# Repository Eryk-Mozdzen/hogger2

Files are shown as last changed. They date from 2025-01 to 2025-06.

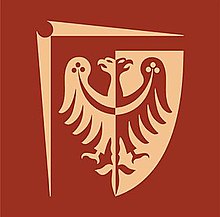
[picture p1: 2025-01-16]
hardware/resources/pwr.jpg

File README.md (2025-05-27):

# Two HOG wheel robot Hogger^2

Hogger^2 is mobile robot with two HOG ([Hemispherical Omnidirectional Gimbaled](https://en.wikipedia.org/wiki/Hemispherical_omnidirectional_gimbaled_wheel)) wheels.

- kinematic models were derived by Paweł Joniak in his [engineering thesis](https://kcir.pwr.edu.pl/~mucha/Pracki/Pawel_Joniak_praca_magisterska.pdf) (2014)
- chassis was originally created by Damian Góral in his [engineering thesis](https://kcir.pwr.edu.pl/~mucha/Pracki/Damian_Goral_praca_inzynierska.pdf) (2017)
- control algorithms were designed by Paweł Joniak in his [master thesis](https://kcir.pwr.edu.pl/~mucha/Pracki/Pawel_Joniak_praca_magisterska.pdf) (2017)
- code generation technique was proposed by Jędrzej Boczar in his [master thesis](https://kcir.pwr.edu.pl/~mucha/Pracki/Jedrzej_Boczar_praca_magisterska.pdf) (2019)
- JSON based communication was proposed by Tomasz Lubelski in his [engineering thesis](https://kcir.pwr.edu.pl/~mucha/Pracki/Tomek_Lubelski_praca_inzynierska.pdf) (2023)

## CAD project

CAD files are developed using Onshape [here](https://cad.onshape.com/documents/57202b77900f6c62ca0efc3a/w/393cd826dd9c91d9b304b9f8/e/825e632008c05703f420ee31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).

## Hardware overview



## Software overview



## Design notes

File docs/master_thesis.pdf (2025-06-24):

## Wrocław University of Science and Technology Faculty of Electronics, Photonics and Microsystems

### Field of Study: Control Engineering and Robotics (AIR)

# MASTER THESIS

## Title of Thesis:

### Control system for two HOG wheel mobile robot

## Author:

### Eryk Możdżeń

## Supervisor:

Robert Muszyński PhD,

### Department of Cybernetics and Robotics

### WROCŁAW 2025

# Contents

1 Introduction | 3
2 Platform description | 5
3 Control algorithms | 27
4 Experiments | 36
5 Summary | 70
Bibliography | 72
A Electronic schematic | 76

Contents | 2
B Motor controller tunning | 84
C Cascade PID tunning | 86

For typesetting this thesis, the LATEX document preparation system has been used. LATEX has been developed by L. Lamport [Lam94], and is an overlay on top of the TEX system [Knu86a, Knu86b]. Mathematical fonts called AMS Euler which have been used in this document, have been commissioned by the American Mathematical Society and designed by H. Zapf [KZ86] with the assistance of D. Knuth and his students. The text font, called URW Palladio, is a clone of the Zapf font family named Palatino [LPn05], and in the author’s opinion, it harmonizes exceptionally well with the design of the AMS Euler font. The authors of the thesis template are R. Muszyński and R. Orozco [MO22], who utilized the mgr.cls document class created by A. Ratajczak [Rat08].

[Knu86a] D. E. Knuth, The TEX book, volume A of Computers and Typesetting. Addison-Wesley, Reading, 1986.

[Knu86b] D. E. Knuth, TEX: The Program, volume B of Computers and Typesetting. Addison-Wesley, Reading, 1986.

[KZ86] D. E. Knuth, H. Zapf, AMS Euler — A new typeface for mathematics. Scholary Publishing, 20:131–157, 1986.

[Lam94] L. Lamport, LATEX: A Document Preparation System. Addison--Wesley, Reading, 1994.

[LPn05] Linotype Palatino nova: A classical typeface redesigned by Hermann Zapf, Linotype Library GmbH, 2005.

[MO22] R. Muszyński, R. Orozco, Examples and formatting guidelines for a
thesis. https://kcir.pwr.edu.pl/~mucha/Pracki/praca_dyplomowa_wzor.
pdf, (https://kcir.pwr.edu.pl/~mucha/Pracki/praca_dyplomowa_wzor.pdf) 2022.

[Rat08] A. Ratajczak, Document class – mgr.cls. http://diablo.kcir.pwr.edu.pl/
~ar/LaTeX/mgr.php, (http://diablo.kcir.pwr.edu.pl/~ar/LaTeX/mgr.php) 2008.

# Chapter 1

# Introduction

Nowadays, mobile robotic systems are widely used to manage warehouses and to support production lines in factories around the world. Robots often operate in well-known environments specifically prepared for their operation, e.g., mobile robots on flat concrete floors in warehouses. In order to perform agile movements on flat ground, it is common to use omnidirectional wheels as the main drive system for UGV platforms [KSBT⁺17].
The Hemispherical Omnidirectional Gimballed (HOG) wheel from 1938 [mec38], called also “Singularity Drive System”, has been a topic of research in robotics applications in the past few years [Ack, Ryb13, Jon14, Jon17, Boc19]. In theory, the use of constantly rotating hemispheres, each with a variable orientation, enables motion with high acceleration in any chosen direction. Additionally, massive hemispheres with high inertia can act as a kinetic energy bank for the platform, allowing the use of less powerful motors without compromising the robot’s agility.
A similar type of propulsion can be observed in power troweling machines, which are widely used in the finishing of concrete surfaces. This branch of the industry has already been robotized, and examples of such robots are presented in Figure 1.1. In contrast, the HOG drive relies on a single point of contact with the ground, which has the advantage of allowing a relatively simple mathematical description of the system. Nevertheless, sufficiently large hemispheres should also operate reliably in muddy and sandy environments, similarly to trowelling machines.
The goal of this thesis is to modernize the existing mechanical design of a two HOG wheel mobile robot, develop a hardware platform that enables the implementation of advanced control algorithms for such a robot, and conduct a qualitative analysis of the performance of selected control algorithms that had previously been tested in simulation environments only. The content of this work is organized as follows. Chapter 2 contains a description of the robot, including mechanical modifications, and custom controller module. The description of the tested algorithms are presented in Chapter 3. Chapter 4 presents the results of the conducted experiments along with detailed conclusions. Chapter 5 contains a summary and the key conclusions drawn from working with the HOG drive technology.

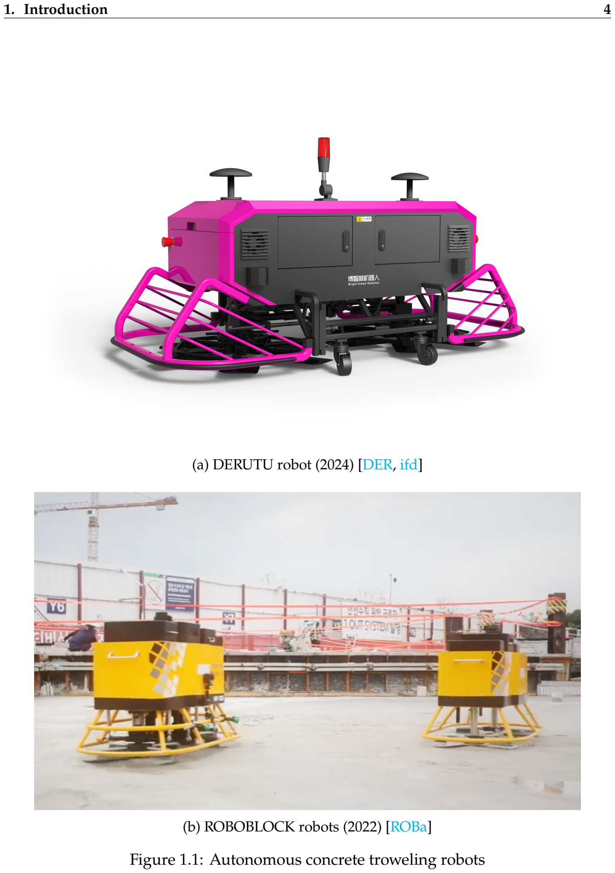
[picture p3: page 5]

1. Introduction | 4
(a) DERUTU robot (2024) [DER, ifd]
(b) ROBOBLOCK robots (2022) [ROBa]

Figure 1.1: Autonomous concrete troweling robots

# Chapter 2

# Platform description

Robots with two HOG wheels are not widely available. For the purposes of this work, the Hogger²
robot (shown in Figure 2.1) originally designed and elaborated as a part of the thesis [Gór17] was expanded and redesigned. This chapter includes the description of the dedicated electronic controller module, the developed software, the mechanical modifications and solutions of other issues identified during the development.
A HOG wheel, shown in Figure 2.2, it a type of drive system that allows movement in any direction using constantly spinning hemisphere, or part of it. In perfect conditions, hemisphere touches the ground in exactly one contact point P. By tilting the axis of rotation from the vertical position by small amount α, one can directly control the point of contact with the ground, effectively creating a wheel with variable radius r, angular velocity ω, and heading (not shown in Figure).
In the Hogger²
robot two HOG wheels are applied with an additional one passive Caster wheel that acts as a third support point. Assuming that the robot moves on a plane, it’s actual pose can be described using the coordinates x and y of the selected HOG wheel contact point and the orientation of the robot body. To obtain a complete robotic platform, it was necessary to equip the robot with perception and control systems.

## 2.1 Requirements, decisions and assumptions

Integrated controller circuit acts as central decision unit mounted on the robot body. First version of the hardware design was developed by the author as part of the “Intermediate Project” course and described in reports [Moż24, Moż25]. Electronics circuits design for the Hogger²
robot is shown in Figure 2.3. The design consist of main microcontroller control unit, actuators for two HOG wheels, sensors needed for environment perception, and additional microcontroller with wireless communication capabilities. The overall design reduced the number of wires between components to a useful minimum. Electronics schematic as well as PCB design of the controller module is attached in Appendix A.
From the control task point of view the robot consists of two BLDC motors, for spinning the hemispheres, and four servomotors, for tilting them. For the sake of simplicity and robustness, it was decided to incorporate the BLDC motor controllers as a part of

2. Platform description | 6

Figure 2.1: The original Hogger² robot [Gór17]

the controller module, rather than relying on off-the-shelf solutions. It was assumed that hemispheres should rotate at relatively high speeds, so a “sensorless” method for driving BLDC motors was selected [LCA]. This approach enables measurement of the motor’s actual velocity without the need to install additional encoders on the motor shaft.
In order to perform advanced trajectory tracking algorithms, information about current position and velocity of the robot and its joints must be available to the robot embedded microcontroller in real time. It was decided that the state vector would be estimated using sensor fusion techniques, without correction from external systems. A further reduction in wiring was achieved by placing most of the sensors inside the controller module itself, creating an all-in-one solution. Both the solutions are described below.

## 2.2 Mechanical modifications

In order to conduct experiments with the existing robotic platform, its components had to be supplemented and modified. Mechanical components added to the robot are shown in Figure 2.4. The optical sensor was mounted into conical part, shown in Figure 2.5, to maximize height above ground without limiting the field of view. The caster wheel, the third support point, was shifted away from the main body of the robot to achieve a stable construction. The 3S LiPo 2000 mAh battery was placed on the center wheel at the back to act as a counterweight to the optical sensor cone located at the front. The controller module casing, shown in Figure 2.6, was mounted on top of the robot using mainly existing mounting points.
The servo drives originally used in the robot were not capable of precise control of the gimbal axes. The PWM interface was not capable of sending telemetry containing the actual position and velocity values of the drives. As a replacement, four Dynamixel AX-12A [ROBb] servomotors were mounted to drive all gimbal axes. In addition, the existing damaged BLDC motors were replaced with KAVAN C2830-750 motors [KAV]. The connection between the motor shaft and the hemispherical wheel, shown in Fig-

2. Platform description | 7
(a) rotation axis is vertical – no movement
(b) small tilt
(c) bigger tilt

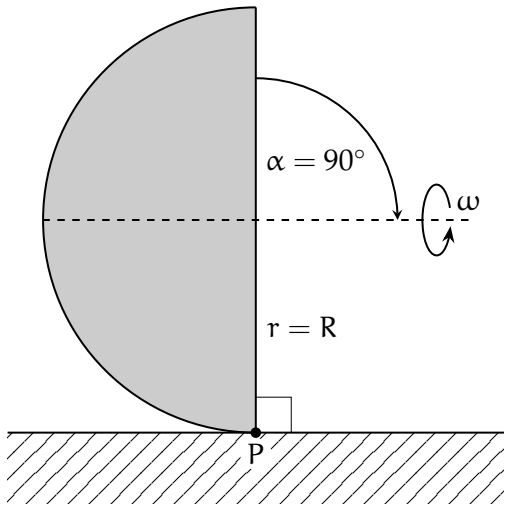
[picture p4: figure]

(d) maximum tilt – standard wheel

Figure 2.2: A HOG wheel tilting principle (cross section)

Figure 2.3: Electronic circuits of the Hogger²

Figure 2.4: Supplemented components

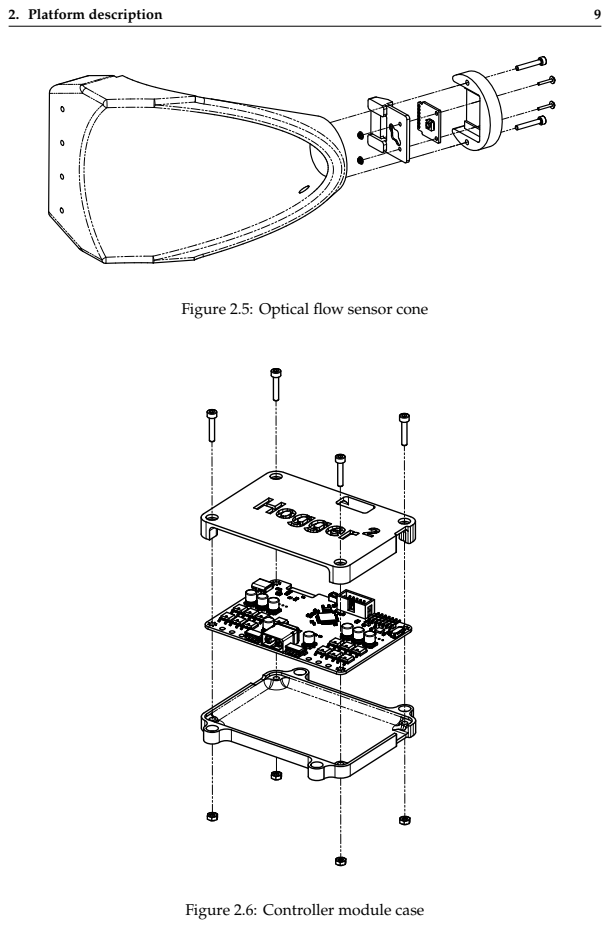
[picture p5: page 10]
2. Platform description

Figure 2.5: Optical flow sensor cone

Figure 2.6: Controller module case

2. Platform description | 10

Figure 2.7: Motor–hemisphere connection

ure 2.7, was redesigned to prevent looseness caused by vibrations. The threaded core allows for easy replacement of the wheel itself, enabling tests of how the hemisphere material affects the robot’s operation for future applications. Both thread directions are opposite to the desired wheel rotation, so the threads cannot unscrew themselves during normal ground operation. The existing silicone hemispheres were severely damaged at the point coinciding with the axis of rotation, so they were replaced with PLA 3D-printed parts. In summary, the mechanical construction is shown in Figure 2.8.

## 2.3 BLDC motor control

Brushless DC (BLDC) motors, due to their high durability, are the standard for modern robotic structures. Unlike conventional brushed motors, they require dedicated control algorithms to produce rotary motion. This section describes the sensorless control method used for the operation of the Hogger²
robot.

### 2.3.1 Source voltage inverters

A BLDC motor can be actuated by applying an alternating voltage pattern, commonly called the “six-step” algorithm [LCA] through its phases (U, V, W) via the source voltage inverter circuit shown in Figure 2.9. For practical reasons, the design consists of six separate power switches, arranged into three pairs (half-bridges) of upper (QUH, QVH, QWH) and lower (QUL, QVL, QWL) transistors. Automotive-grade IPD90N04S4L-04 N-channel MOSFETs [Inf] were used, along with LM2105D gate drivers [Ins] (not shown in Figure). Each half-bridge needs to be controlled by a pair of coupled PWM signals, resulting in a total of 12 control variables for both motors. To meet these requirements, the STM32H523 [STM] microcontroller was selected as a main control

2. Platform description | 11

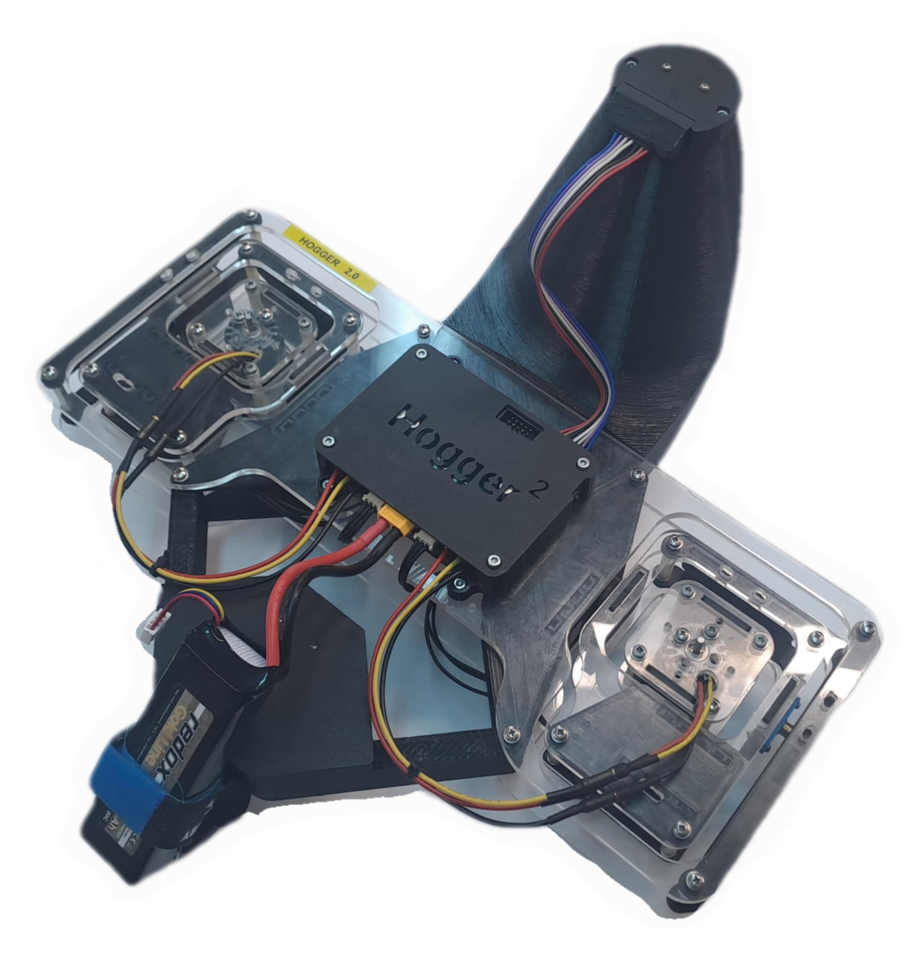
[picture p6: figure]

Figure 2.8: The Hogger²
robot after modifications

Figure 2.9: Source voltage inverter

2. Platform description | 12

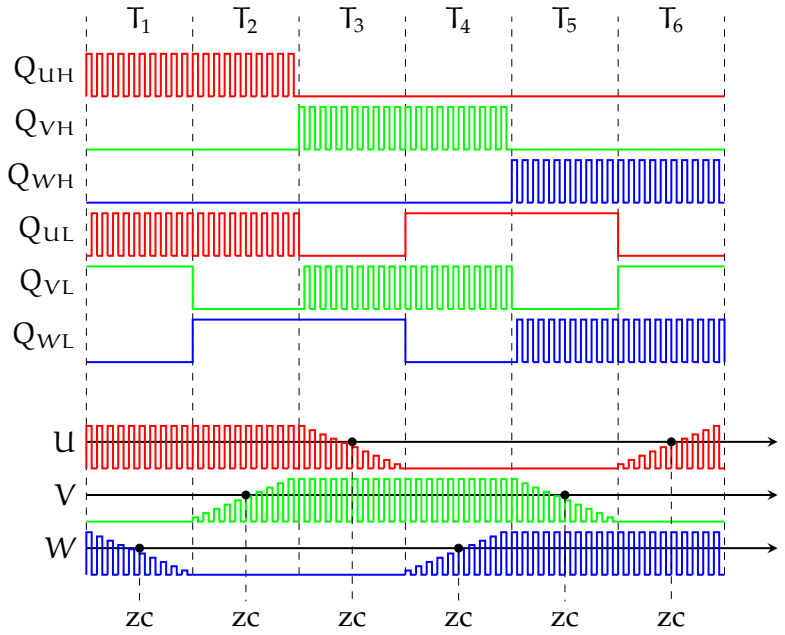
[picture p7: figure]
QUH; QVH; QWH; QUL; QVL; QWL

Figure 2.10: Six-step algorithm with back-EMF zero cross events

unit, as it includes two Advanced Control Timer peripherals dedicated to motor control applications.
The six-step algorithm, shown in Figure 2.10, considers an ordered sequence of control permutations T for switches Q. To obtain rotary motion, all steps must be applied in the sequence T1, T2, . . . , T6, T1, . . . for clockwise rotation, or T6, T5, . . . , T1, T6, . . . for counterclockwise rotation. Each step, also called a commutation, can configure each pair QxH and QxL to:
- connect the motor phase to the supply voltage (QxH high, QxL low),
- connect the motor phase to the ground (QxH low, QxL high),
- left the motor phase floating (QxH and QxL low).

Closing the upper and lower switches of the same half-bridge at the same time creates a short circuit and may damage the transistors. To prevent this situation, an additional 2 µs dead time was configured in the peripheral settings. In each step, one motor phase is powered, one is connected to ground, and the remaining floating phase is used to determine the next step through signal conditioning. For smooth control of the powered phase, 50 kHz center-aligned PWM modulation is applied to the upper and lower switches. Figure 2.11 presents oscillograms of phase and control signals for selected angular velocities. The described method aims to obtain a trapezoidal phase voltage waveform. In practical applications, the minimum angular velocity that the motor controller can handle is 125 rad

s without load, and 200 rad
s

during robot operation.
The maximum velocity is constrained by the motor itself. Empirical tests have shown that when the PWM duty cycle exceeds 80% with load, the motor begins to overheat significantly.

2. Platform description | 13
(a) angular velocity 200 rad
s
(b) angular velocity 250 rad
s
(c) angular velocity 500 rad
s
(d) angular velocity 664 rad
s

(80% duty cycle)

Figure 2.11: Oscillogram of QUH (yellow), QUL (blue), and U phase (red)

### 2.3.2 BEMF signal conditioning

Proper motor operation highly depends on the timing of the switching steps in the six-step algorithm. The rotor of the BLDC motor consists of an even number of magnets, forming an alternating magnetic field. By performing steps from T1 to T6, the rotor rotates through an angle called an electrical rotation, defined by one pair of magnets. To achieve a full 360◦ movement, called a mechanical rotation, the six-step algorithm must be performed n times (n electrical rotations), where n is the number of pole pairs in the rotor.
Each step represents ¹/6 of an electrical rotation, which equals 60◦
. During each step,
one winding coil is left floating, and the rotating magnets of the rotor induce a back electromotive force (BEMF) in it. Unfortunately, the BEMF voltage level is proportional to the angular velocity of the rotor, which implies that practical signal conditioning is only possible above a minimum shaft velocity. According to [LCA], the best motor performance is achieved by keeping the point where the BEMF voltage crosses the voltage at the motor’s coil interconnection (point N in Figure 2.9) in offset of 30◦ from
the beginning of each step. This point is called the zero-crossing event (ZC) and its precise localization is the greatest difficulty during implementation of the algorithm. The BEMF signal can be observed from the U, V, and W phases by the control unit using ADC through resistor dividers and small filtering capacitors. The neutral voltage

2. Platform description | 14

Timer; Advance Control Timer; ADC; six-step algorithm; PID; signal conditioning; Firmware; Peripherals; Update Event; Commutation Source; External Trigger Source; step duration; velocity; PWM duty cycle; step config; Commutation ISR; Injected Conversion Complete ISR; QVH; QUL; QUH; QVL; QWH; QWL

Figure 2.12: Controller implementation on the STM32H5

at point N can be calculated as the average of phase voltages

UN =

U + V + W
3

Controller implementation is presented in Figure 2.12. The STM32 ADC peripheral was synchronized with Advanced Control Timer to perform conversion in the middle of PWM high period using “Injected Conversion” feature. Then, on each PWM period, voltage from appropriate floating phase is compared with UN voltage by the software. To prevent false positive detections, the majority filter described in [LCA] was implemented. Result of each comparison is stored in the 8-bit variable acting as a shift register. If the number of positive comparisons (ones) is greater than the predefined threshold kth, then the ZC event occurs roughly 1
2

kthTPWM before the conversion starts. Using this knowledge, it is possible to calculate the time of next commutation in the sequence.
Unfortunately, under high motor load fluctuations experienced during movement using hemispheres, additional filtering was needed. In summary, period ti+1 of the next commutation Ti+1 can be calculated as

tizc = tconv −

1
2

kthTPWM

ti+1ideal = 2tizc

ti+1 = αtti+1ideal + (1 − αt)ti

,

where tconv is conversion start time (counted from the beginning of the step Ti), tizc is ZC event occur time, ti+1ideal is theoretical duration of next commutation, and ti+1 is duration that is applied in reality. For motors KAVAN 2830 750 KV parameters kth = 4, αt = 0.05 were found empirically.

2. Platform description | 15

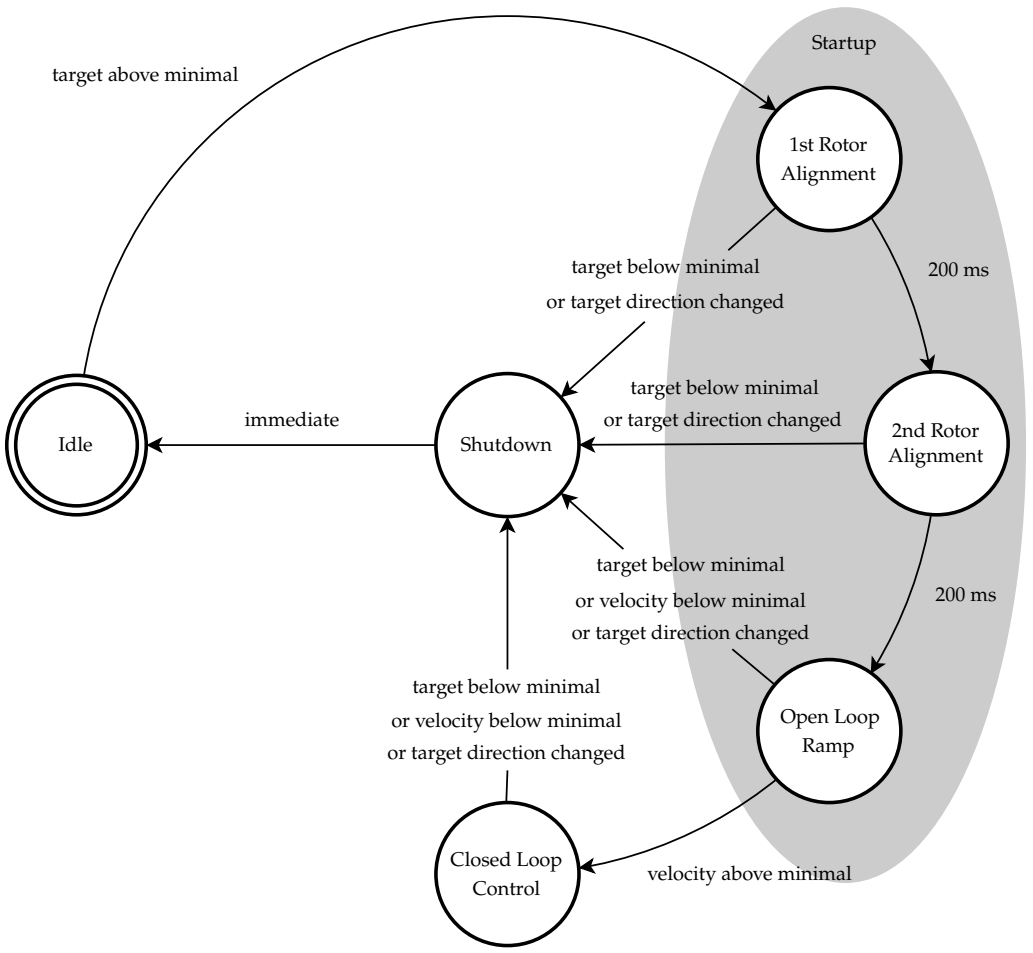
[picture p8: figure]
Idle; Open Loop Ramp; Closed Loop Control; Shutdown; Startup; 1st Rotor Alignment; 2nd Rotor Alignment; target above minimal; velocity above minimal; target below minimal; or velocity below minimal; or target direction changed; immediate

Figure 2.13: Motor controller state machine

Mechanical angular velocity of the motor shaft ω can be calculated and filtered by

ωzc = 2π

nzc

6pTzc
ωi+1 = αωωzc + (1 − αω)ωi

,

where ωzc is instantaneous angular velocity, ωi is filtered angular velocity, p is number of rotor pole pairs, and nzc is number of ZC events observed in time Tzc. For the selected motors p = 7, and empirical tests shown that parameters Tzc = 20 ms, αω = 0.1 are giving sufficiently good performance in practice.

### 2.3.3 Startup and closed-loop operation

The motor controller logic, presented in Figure 2.13, is defined by a finite state machine that handles motor startup, operation, and shutdown. The startup procedure consists of rotor alignment phases followed by a velocity ramp controlled in open-loop mode. The first rotor alignment stage sets the rotor to a known position by applying predefined commutation T1 for a specified duration. The second alignment ensures that

Figure 2.14: Geometric properties of the step response of an inertial system

the rotor spins in the correct direction by applying commutation T1 or T5, according to the desired direction. Both are performed using a PWM duty cycle of u = 30% over a 200 ms period.
When alignment is complete, a startup ramp is applied to accelerate the rotor to a point where BEMF signal conditioning becomes feasible. Subsequent commutations are applied to the inverter circuit, each with increasing frequency f and a constant PWM duty cycle of u = 40%. The ramp curve is defined as

f(t) = fmax
1 − e

−λt
,

where fmax = 1 kHz is the maximum commutation frequency, λ = 1 is the acceleration parameter, and t is the time elapsed since the beginning of the ramp. Empirical tests have shown that the proposed ramp provides more robust results than linear ramps and that the correct ramp shape is key to a successful startup. To ensure a smooth transition between open-loop and closed-loop control, a special blending function is used to merge both signals over a 1 second period after the ramp is complete.
The closed-loop operation is performed using a PID controller to maintain the motor’s angular velocity at the target value, using the PWM duty cycle u as the control input. For each motor, a PID controller was tuned using the Chien-Hrones-Reswick (CHR) method with 20% overshoot [ÅH95]. The results of the tuning procedures are included in Appendix B. The method, shown in Figure 2.14, involves drawing additional straight lines onto the step response (red plot) of an unknown inertial system, representing:
- the signal level at steady state before applying the step,
- the signal level at steady state after applying the step,
- the tangent line with the maximum slope (at point B).

Analysis of the line intersections reveals the basic geometric properties K (gain), T (time constant), and L (lag) of the simplified system, which approximates the plant.

2. Platform description | 17

These properties can be used to calculate PID parameters that ensure good closed-loop performance using the CHR 20% overshoot formulas

Kp = 0.95 T
KL
Ki = 0.68 1
KL
Kd = 0.45 T
K

To automate the process of obtaining PID settings from the step response, a Python script was created to find the parameters of the best-fitting four-parameter model in the form
Hm(s) = | Km (T1ms + 1)(T2ms + 1)
e

−Lms
,

which step response in the time domain is given by

hm(t) =

0 | t ⩽ Lm

Km

1 +

T2me

− t−Lm

T2m | − T1me − t−Lm
| T1m
T1m − T2m

!
| t > Lm

,

where T1m and T2m are time constants, Lm is a delay, and Km is the model gain. Using this model, it is possible to algebraically determine the point B, and ultimately extract the K, T, and L properties.

## 2.4 Sensor fusion

Reliable knowledge about robot state is a key to precise control. The robot x, y, θ coordinates are not possible to measure directly without external reference systems like GNSS or radio anchors [KCB⁺23]. Sensor fusion techniques allows for obtaining information about the system state from multiple measurement sources which is more reliable than each of the measurements separately. In this work an Extended Kalman Filter has been used for this purpose.

### 2.4.1 Extended Kalman Filter

In order to estimate the 2D pose of the robot using only on-board sensors, Extended Kalman Filter (EKF) [Wika] was developed. EKF is a sensor fusion technique that enables the estimation xˆ of the unknown state x of the discrete system in the form
xk = f(xk−1,uk−1) + ωk−1
zk = h(xk) + vk

,

where u are the system inputs, z are the measurements, and ω and v are process and observation noises, both assumed to be zero-mean Gaussian. In the following

2. Platform description | 18

description it is assumed that the system operates at fixed time intervals ∆t between time steps k.
The algorithm consists of two steps: prediction and correction. The prediction step can be defined as
xˆk|k−1 = f(xk−1|k−1,uk−1)
Pˆ
k|k−1 = FkPˆ
k−1|k−1F

T
k + Qk−1

,

where

Fk =

∂f
∂x
xˆ k−1|k−1
,uk

,

f is the system model, Q is the process noise covariance matrix, and Pˆ is the estimate of state vector covariance matrix. The notation xn|m represents the value of x at time n given observations from time periods where m ⩽ n. In this step, the input vector u can be obtained from sensors recording of relatively high-frequencies. It is crucial to perform the prediction step at fixed time intervals. Unfortunately, this implies prediction frequency to be equal to the sampling frequency of the slowest predicting sensor.
The correction step can be defined as
xˆk|k = xˆk|k−1 + Kk(zk − h(xˆk|k−1))
Pˆ

k|k = (I − KkHk)Pˆ
k|k−1

,

where
Kk = Pˆ

k|k−1Hk(HkPˆ
k|k−1H

T
k + Rk)

−1
,

Hk =

∂h
∂x
xˆ k|k−1

,

h is the sensor model, and R is the sensor noise covariance matrix. As opposed to the prediction step, the correction step can be performed separately for each correcting sensor. This effectively enables operation at the full sampling frequency of each sensor. Correcting measurements represent relatively low-frequency signals.

### 2.4.2 Estimator implementation

For the Hogger²
robot, the state vector x we will define as

x =

p θ p˙ θ γ ˙ m

T
=

x y θ x˙ y˙ θ γ ˙ m

T
,

where p with components x, y represents the robot’s position, and θ represents the robot’s orientation. Apart from that, due to the practical reasons it is common to incorporate environment depended system model parameters into the state vector itself. Here such an element is γm that represents the angle of magnetic inclination related to the magnetometer sensor model (described in paragraph below “Magnetometer model”).

2. Platform description | 19

System model

The system model consider inputs u in the form

u =

ax | ay | ωz | ω˙ z

T
,

where ωz is gyroscope measurement of robot’s angular velocity, and ˙ωz is angular acceleration computed numerically. Terms ax, ay are linear components of acceleration vector a observed in accelerometer’s frame located with offset ra

ra = | -
rax | rayT

from the robot’s frame origin. Acceleration and angular velocity measurements comes from MPU6050 IMU sensor [Inv], with sampling frequency 1 kHz.
To model the system, rotational movement can be approximated as a uniform rotational motion in the form of
θk = θk−1 + ∆tθ˙
| | | k−1,
where ∆t is a short time interval equal to IMU sampling period. Analogously, position p can be approximated using uniformly accelerated motion in the form of

pk = pk−1 + ∆tp˙ k−1 +

1
2

∆

2
tp¨ k−1
,

p˙ k = p˙ k−1 + ∆tp¨ k−1
,

where p¨ is the robot’s acceleration expressed in the world’s reference frame. An accelerometer mounted on the rotating body senses acceleration a expressed as

a = ab + ac + at,

where
ac = ω × (ω × ra)
at = α × ra

,

ab is acceleration of the body itself, ac is centripetal acceleration due to rotational movement ω = [0 0 θ˙
]

T
, and at is tangential acceleration due to presents of angular acceleration α = [0 0 ˙ωz]

T
. All of them are expressed in the accelerometer’s reference frame. The robot’s acceleration in the world’s frame can be defined as

p¨ =

cos θ − sin θ
sin θ cos θ

# abx

aby

In summary, the system model f is defined as

f(x,u) =

x + ∆tx˙ +

1
2∆

2
t

(abx cos (θ) − aby sin (θ)) y + ∆ty˙ +

1
2∆

2
t

(abx sin (θ) + aby cos (θ)) θ + ∆tθ˙
x˙ + ∆t (abx cos (θ) − aby sin (θ)) y˙ + ∆t (abx sin (θ) + aby cos (θ)) ωz
γm

,

where abx = ax + raxθ˙ 2 + ω˙ zray, and aby = ay + rayθ˙ 2 − ω˙ zrax.

2. Platform description | 20

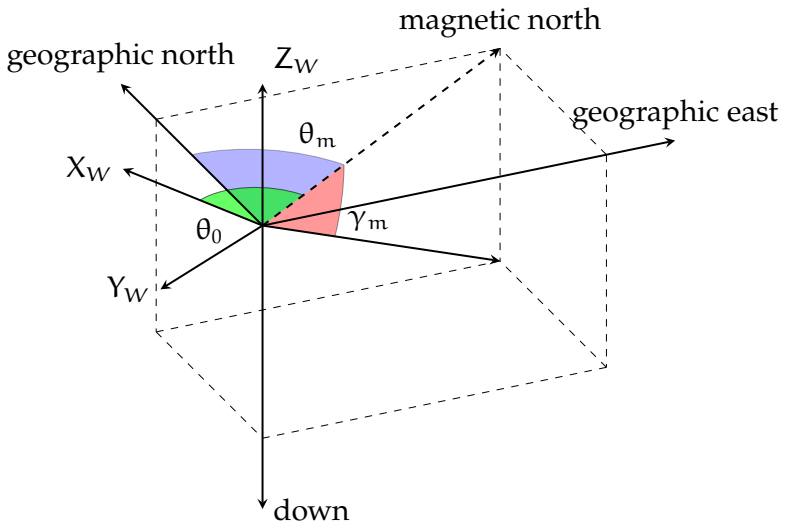
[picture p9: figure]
geographic east; geographic north; down; magnetic north

Figure 2.15: Earth’s magnetic field direction

Magnetometer model

Relying only on dead-reckoning using gyroscope measurements is not robust enough to obtain reliable information about the robot’s orientation. Sensor HMC5883L [Hon], with a sampling frequency 200 Hz, was introduced as a magnetic north orientation reference.
Earth’s magnetic field, illustrated in Figure 2.15, is not identical at every point on the globe and it has two properties: the declination angle θm and the inclination angle γm. Magnetic declination θm is the deviation angle from the true geographic north. During the robot operation, it is helpful to set an artificial declination θ0 (see Figure 2.15) to align the world’s reference frame XWYWZW with the environment (e.g., building walls). Magnetic inclination γm is the deviation angle from the horizontal plane. Estimation of inclination allows the system to adapt to the changing environment in which the robot operates. Using this knowledge, the magnetometer model can be expressed as

hmag(x) =

mx
my
mz
- =

cos (θ + θ0) sin (θ + θ0) 0 − sin (θ + θ0) cos (θ + θ0) 0
0 | 0 | 1

cos γm
0
sin γm
- ,

where mx, my and mz are components of the normalized magnetic field vector.

Optical flow sensor model

Velocity correction is performed using the optical motion sensor PMW3901 [Pix], commonly called “optical flow” sensor. The sensor is capable of measuring ∆px and ∆py pixel shifts between frames with a 50 Hz sampling frequency. Measurements are expressed in the camera frame, which is located at an offset rf

rf =

rfx rfyT

2. Platform description | 21

from the robot’s frame origin. Using the technique described in [Jac21] it is possible to define the relation between robot’s velocities and ∆p as

hflow(x) =
∆px
∆py
= ∆tf

ff
hf

cos θ sin θ
− sin θ cos θ

x˙
| y˙
| +

| −rfyθ˙ rfxθ˙
,

where ff is the focal length of the lens, hf is the sensor’s height above the ground, and ∆tf is sensor sampling period.

### 2.4.3 Sensor calibration

Measurement models from the previous section describe the behavior of ideal sensors. Unfortunately, this does not hold for the low-cost MEMS elements used in this system. This section describes techniques to increase the reliability of these measurements.

Gyroscope calibration

Simple MEMS gyroscopes are susceptible to bias drift (also known as zero-drift phenomenon). Temperature changes cause unwanted variations in the gyroscope’s output, even when it is not experiencing actual angular motion. To compensate for this drift, the raw measurement values ωraw for each axis are averaged over a stationary period of approximately 10 seconds. The resulting bias is then subtracted from the raw values, as shown below:

ωcomp = ωraw − ωraw.

This calibration procedure should be performed before each experimental session.

Accelerometer calibration

As with the gyroscope, the zero-drift phenomenon is also present during the operation of the accelerometer. To further increase the reliability of the measurements, a full 3D rotation, translation, and scaling can be applied to the raw sensor outputs as follows:

acomp = Maaraw + ba,

where Ma is the combined rotation and scale matrix, and ba is the offset vector. Both parameters can be obtained using the least-squares method
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
where

Ja =

x1 | y1 | z1 | 1
x2 | y2 | z2 | 1
x3 | y3 | z3 | 1
xN | yN | zN | 1

, | K =

X1 | Y1 | Z1
X2 | Y2 | Z2
X3 | Y3 | Z3
XN | YN | ZN

,

2. Platform description | 22

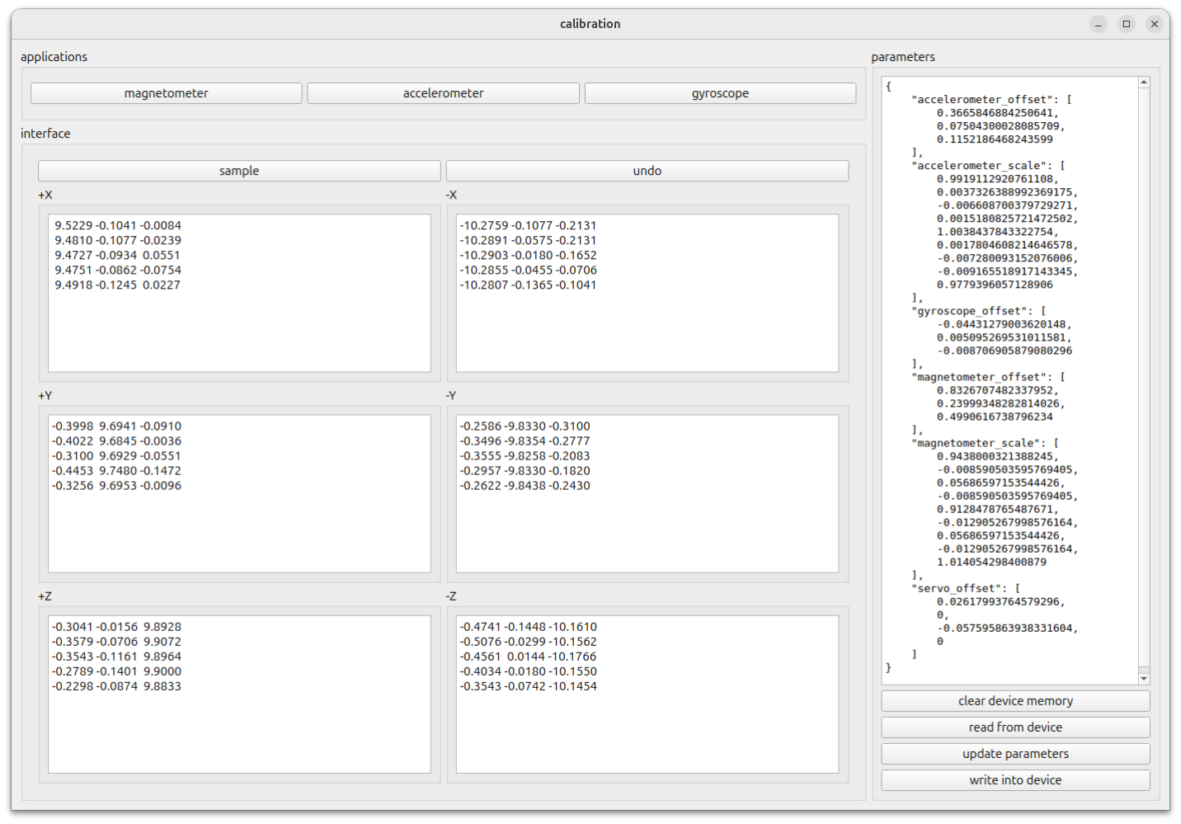
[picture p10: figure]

Figure 2.16: Accelerometer calibration app

xi, yi, and zi are the elements of the i-th araw sample, Xi, Yi, and Zi are the elements of the corresponding reference acceleration vector aref, and N is the number of collected samples. The simplest reference accelerations can be obtained by using gravity:

aref ∈

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
where g is a value of Earth’s gravity acceleration.
For practical reasons, a dedicated PC application for performing sensor calibration, with interface shown in Figure 2.16, was created using the Qt6 [Gro] and Eigen [JG] libraries in C++. The procedure involves placing the robot in six different orientations using, e.g., flat mechanical fixtures on a level surface. Typically, collecting three to five samples in each reference direction is sufficient to achieve satisfactory calibration results.

Magnetometer calibration

A magnetometer placed inside the robot’s frame senses a distorted magnetic field. According to [Ozy], there are two kinds of magnetic distortion: soft-iron and hard-iron distortions. Soft-iron distortions are related to scaling of the resulting vector. Hard-iron distortions offset all measurements by a constant vector. In practical applications, it is necessary to compensate for the influence of both of these phenomena. Translation and

2. Platform description | 23

scaling can be applied to the raw sensor outputs in the following way:

mcomp = Mmmraw + bm,

where Mm is the combined rotation and scale matrix, and bm is the offset vector. Both can be obtained by collecting a dataset of raw measurements and fitting an ellipsoid to it in standard form

p1x

2 + p2y

2 + p3z

2 + p4xy + p5yz + p6zx + p7x + p8y + p9z + 1 = 0,

where pi,i = 1, . . . , 9 creates the ellipsoid coefficients vectorp. Thus, the above equation can be rewritten into
Jmp = 0,

where

Jm =

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
| x1y1 | y1z1 | z1x1 | x1 | y1 | z1 | 1
x

2
2 y

2
2

z

2
2 | x2y2 | y2z2 | z2x2 | x2 | y2 | z2 | 1
x

2
3 y

2
3

z

2
3 | x3y3 | y3z3 | z3x3 | x3 | y3 | z3 | 1
x

2
N y

2
N z

2
N | xNyN | yNzN | zNxN | xN | yN | zN | 1

,

with xi, yi, and zi being the elements of the i-th mraw sample, and N the number of collected samples in the dataset. To achieve good fitting performance, Singular Value Decomposition (SVD) [Wikc] was used to decompose Jm into three matrices

Jm = UΣVT
,

where U is the matrix of left singular vectors, Σ is the diagonal matrix of singular values, and V is the matrix of right singular vectors. The null-space solution p is given by the singular vector corresponding to the smallest singular value, which is usually the last column of V.
Like for the other sensors, the PC calibration app contains a magnetometer calibration feature, as shown in Figure 2.17. To simplify the interface, magnetometer samples are presented as three planar projections: XY (red), YZ (green), and ZX (blue). The left plot shows the samples before calibration (dataset), while the right plot visualizes the data after transformation. Both charts are updated in real time for every telemetry frame received from the robot. The calibration procedure involves rotating the robot in space until the points of different colors on the right plot overlap. This indicates that the transformation has converged and the calibrated samples lie on a sphere.

## 2.5 Communication

Reliable communication with robot subsystems is an important requirement during debugging and supervision, even for autonomous robots. The Hogger²
robot is
equipped with an ESP32C3 microcontroller to ensure wireless communication between the main control unit (STM32) and a PC. Figure 2.18 presents the STM32-PC communication channel. In [Lub23] it is proposed to apply a JSON-based communication

2. Platform description | 24

Figure 2.17: Magnetometer calibration app

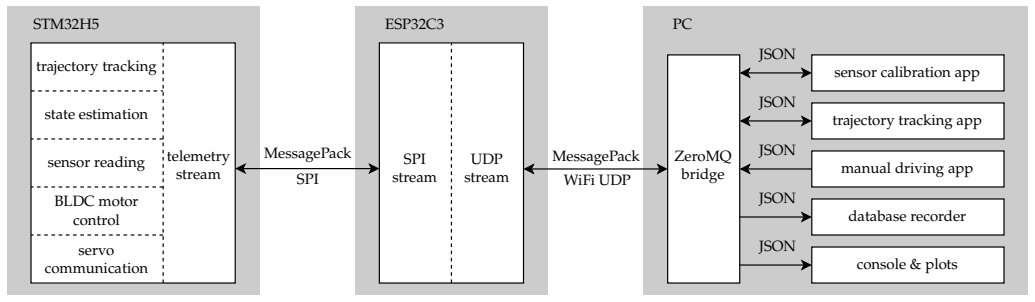
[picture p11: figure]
state estimation; trajectory tracking; MessagePack; SPI; WiFi UDP; sensor calibration app; JSON; trajectory tracking app; manual driving app; database recorder; console & plots; sensor reading; UDP; stream; SPI stream; telemetry stream; BLDC motor control; servo communication; ZeroMQ bridge; STM32H5; ESP32C3

Figure 2.18: Robot communication channel

2. Platform description | 25

protocol [Wikb]. This solution allows sending messages with a complex and nested structure without the need for schema files. To further increase bandwidth, it was decided to use the MessagePack [Fur] format, which is used as a binary equivalent to JSON.

### 2.5.1 Connection between main and network microcontrollers

The main microcontroller is connected to the network microcontroller using the 4-wire SPI bus, where the STM32 is the master and the ESP32 is the slave. In addition, the HANDSHAKE signal is used to indicate the slave’s readiness for the next SPI transaction. The transactions, each with a size of 2 kB in both directions, are performed continuously and consist of:

- 2-byte header – number of valid bytes in the payload,
- 2046 bytes of payload.

This structure ensures that the transaction size is constant, greatly simplifying the logic on both sides and enabling DMA support. The bus clock is set to 31.25 Mbps, exceeding the capabilities of the WiFi driver on the ESP32, which claims to support up to 30 Mbps of UDP throughput under ideal conditions. MessagePack messages are parsed using the cmp library [Gun] for the C programming language.

### 2.5.2 Communication between robot and station

The on-board ESP32 acts as an intermediary between the robot’s logic (STM32) and a PC. The ESP32 works as a WiFi station and connects to a nearby network with the predefined SSID. Data received over SPI is redirected to the predefined network socket, and vice versa. For further increase channel bandwidth, UDP transmission stream is used in both directions.
In case of connection loss with the station, the ESP sends a special stop message to the host to ensure that the robot’s actuators will halt. Conversely, if a timeout occurs on the host, the ESP informs the station about the error.

### 2.5.3 ZeroMQ bridge

Endpoint apps running on the station PC can send and receive data to and from the robot through a dedicated ZeroMQ bridge [zer]. The major purposes of the bridge are:

- maintaining network connection with a robot,
- reading and writing data to ZeroMQ network,
- converting messages between JSON and MessagePack formats,
- collecting throughput statistics.

2. Platform description | 26

This solution allows multiple dedicated apps to run in parallel for plotting or sending commands, while maintaining messages in a human-readable form. ZeroMQ libraries are available in many programming languages, so endpoint apps can be written in languages such as Python or C++.

# Chapter 3

# Control algorithms

Due to its unconventional drive system, the Hogger²
robot still does not have welltested control methods. In recent years, simulation research took place as part of several theses [Jon17, Boc19]. This chapter describes previously designed control algorithms as well as new approaches to controlling the Hogger²
robot.
All algorithms consider robot’s reference frame and gimbal angles like shown in Figure 3.1. Origin of the robot’s reference frame XBYBZB is placed in the point of two gimbal axes ϕ1 and θ1 crossing. The positive end of the XB axis is directed toward the front of the robot, while the positive end of the YB axis represents the left side of the robot’s body.

## 3.1 Simultaneous algorithm

The simultaneous algorithm, originally introduced in [Jon17], assumes same control signals for both HOG wheels. Additionally, it is assumed that the gimbal movement of the hemisphere has no influence on the robot’s body movement. The system can be expressed as

x˙ = Rψ˙ u (cos θ cos θu sin ϕu + sin θ sin θu) y˙ = Rψ˙ u (sin θ cos θu sin ϕu − cos θ sin θu) θ˙ = 0

,

where ϕu and θu are the gimbal control angles, and ψ˙ u is the angular velocity of the hemisphere. Unfortunately, this strategy disables control of the robot’s orientation θ, leaving only position control. The control signals for both wheels can be either identical or mirrored. The identical control signals are given by

ϕu = ϕ1 = ϕ2 = arcsin
−

x˙ ref
Rψ˙ u cos θu

θu = θ1 = θ2 = arcsin
−

y˙ ref
Rψ˙ u

ψ˙ u = ψ˙

1 = ψ˙
2 = const

,

3. Control algorithms | 28

ZW

Figure 3.1: Robot reference frame and gimbal angles

while the mirrored control signals are given by

ϕu = ϕ1 = −ϕ2 = arcsin
−

x˙ ref
Rψ˙ u cos θu

θu = θ1 = −θ2 = arcsin
−

y˙ ref
Rψ˙ u

ψ˙ u = ψ˙

1 = −ψ˙
2 = const

,

where ˙xref and ˙yref are the reference velocities expressed in the robot’s reference frame. The naive control law for the reference velocities was defined as
x˙ ref

y˙ ref
=
cos θ sin θ
− sin θ cos θ

x˙ d
y˙ d
− k
x − xd
y − yd

,

where xd and yd are the components of the desired trajectory, and k is a positive constant gain.

## 3.2 JPTD algorithm

The JPTD algorithm, originally introduced in [Jon17], is illustrated in Figure 3.2. It considers the configuration vector q defined as

q =

x y θ ϕ1 | θ1 | ψ1 | ϕ2 | θ2 | ψ2

T
,

where x, y, and θ represent the robot’s body position and orientation in the world reference frame XWYWZW. The angles ϕi, θi, and ψi, i = 1, 2 fully describe the configuration of each HOG wheel. The robot kinematics can be modeled as a driftless system in the form
q˙ = G(q)η,

3. Control algorithms | 29

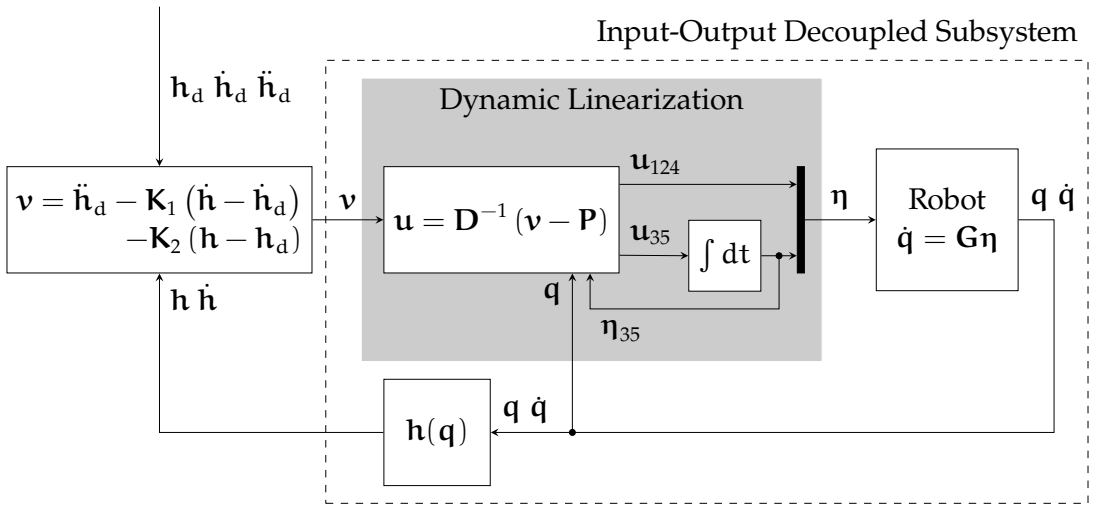
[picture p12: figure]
Input-Output Decoupled Subsystem; Dynamic Linearization; Robot q˙ = Gη

Figure 3.2: JPTD input-output decoupling with dynamic feedback linearization

where
η =

ϕ˙

1 | θ˙
1 | ψ˙
1 | θ˙
2 | ψ˙
2

T
,

and G is a simplified kinematic control matrix obtained in [Jon14]. The full kinematic model Gfull is derived from the nonholonomic constraints and is given as

Gfull(q) =

Rsθ | Rcθcϕ1 | R (sθsθ1 − cθsϕ1
cθ1
) | 0 | 0
−Rcθ | Rsθcϕ1 | −R (cθsθ1 + sθsϕ1
cθ1
) | 0 | 0
0 | −
| R 2L cϕ1

R
2L
| | sϕ1

cθ1

R
2L

cϕ2 −

R
2L
| | | | sϕ2

cθ2
1 | 0 | 0 | 0 | 0
0 | 1 | 0 | 0 | 0
0 | 0 | 1 | 0 | 0
1 | 0 | sθ1 | 0 | −sθ2
0 | 0 | 0 | 1 | 0
0 | 0 | 0 | 0 | 1

,

where sx = sin x, cx = cos x, R is the radius of the hemispheres, and L is half the distance between the centers of the hemispheres. This model can be simplified by removing the influence of the hemisphere tilting angles on the robot’s body movement, resulting in the reduced form

G(q) =

0 | 0 | R (sθsθ1 − cθsϕ1
cθ1
) | 0 | 0
0 | 0 | −R (cθsθ1 + sθsϕ1
cθ1
| | ) 0 | 0
0 | 0

R
2L
| sϕ1

cθ1

0 −

R
2L
| | | sϕ2
cθ2
1 0 | 0 | 0 | 0
0 1 | 0 | 0 | 0
0 0 | 1 | 0 | 0
1 0 | sθ1 | 0 | −sθ2
0 0 | 0 | 1 | 0
0 0 | 0 | 0 | 1

,

3. Control algorithms | 30

where the highlighted elements were replaced by zeros.
Trajectory tracking is achieved using the input-output decoupling technique with dynamic feedback linearization [TM17]. The linearizing output function h is defined as
h(q) = -x y θ ψ1 ψ2

T

By differentiating and factorizing this output, one can obtain the matrix D and the vector P, which satisfy
h¨ = Du + P,

where
u =
η1 | η2 | η˙ 3 | η4 | η˙ 5

T

is the internal control input with additional dynamics introduced. The problem can be reformulated as the task of controlling a double integrator system by introducing a new control signal v
v = h¨.

The trajectory tracking algorithm for such a system is defined as

v = h¨
d − K1

| h˙ − h˙ | d
− K2 (h − hd),

where hd is the desired output of the system, and K1, K2 are positive definite gain matrices. To convert the linearized control signal v into the original input u, the following transformation is applied

u = D⁻¹
(v − P).

In summary, the following expressions were obtained during the above derivation:

D(q, η35) =

−Rη3cϕ1 cθ1 cθ | Rη3 (cθ1 sθ + cθsϕ1 sθ1
) | R (−cθ1 cθsϕ1 + sθ1 sθ) | 0 | 0
−Rη3cϕ1 cθ1 sθ | Rη3 (−cθ1 cθ + sϕ1 sθ1 sθ) −R (cθ1 sϕ1 sθ + cθsθ1
) | 0 | 0

R(η3cϕ1
cθ1−η5cϕ2

cθ2 )
2L | −
| Rη3sϕ1

sθ1

| 2L | Rcθ1 sϕ1
| | 2L | Rη5sϕ2

sθ2
2L | −
| | | | Rcθ2

sϕ2
| | | | 2L
0 | 0 | 1 | 0 | 0
0 | 0 | 0 | 0 | 1

,

P(q, η35) =

R²η3

η3c

2
θ1

s

2
ϕ1

sθ+η3cθ1

cθsϕ1

sθ1

−η5cθ1

cθ2

sϕ1

sϕ2

sθ−η5cθ2

cθsϕ2

sθ1

2L
R²η3
−η3c

2
θ1

cθs

2
ϕ1

+η3cθ1

sϕ1

sθ1

sθ+η5cθ1

cθ2
cθsϕ1

sϕ2−η5cθ2
sϕ2
sθ1

sθ

2L
Rη5cϕ2

cθ2

(−η3sθ1
+η5sθ2

)

2L
0
0

Analysis of the determinant of the matrix D

det D = −

R

3η

2

3η5 cos ϕ1 cos² θ1 sin ϕ2 sin θ2 2L
shows that singularities arise when any HOG wheel halts, or when the right HOG wheel moves purely along one axis of the robot’s reference frame XBYBZB, or when the right HOG wheel is set to vertical. For this reason, special constraints need to be applied to the desired trajectory hd to avoid these singularities.

3. Control algorithms | 31

## 3.3 JPTD–1D algorithm

As an alternative to the JPTD algorithm, an even more simplified method was proposed. The two HOG wheel robot can be reduced to a (2,0) robot by considering θ1 = 0, θ2 = 0, and ψ1 = −ψ2 = ψ which gives the configuration vector q as

q =

x y θ ϕ1 | ϕ2 | ψ

T

Then, the driftless system can be rewritten using

η =

ϕ˙

1 | ϕ˙
2 | ψ˙

T
| | ,

and

G(q) =

0 0 | −R cos θ sin ϕ1
0 0 | −R sin θ sin ϕ1
0 0 R
2L
| sin ϕ1 + R 2L sin ϕ2
1 0 | 0
0 1 | 0
0 0 | 1

The linearizing output function h was selected as

h(q) =

x + d cos θ
y + d sin θ
ψ
- ,

where d is length of the “virtual shaft”. It should be noted that, since the robot cannot move sideways in this method, the virtual shaft represents a point in front of the robot with which the algorithm is able to track the trajectory. Additionally, due to the smaller number of control inputs, trajectory dimensionality is reduced, and direct control over θ is lost.
Input-output decoupling is obtained in the same way as in the JPTD algorithm, but u is redefined as
u =
η1 | η2 | η˙ 3

T

In summary, the following expressions were obtained during the above derivation:

D(q, η3) =

−

Rη3cϕ1

(2Lcθ+dsθ)
2L | −

Rη3cϕ2
dsθ
2L

R(−2Lcθsϕ1
−dsθ(sϕ1
+sϕ2

))

2L
Rη3cϕ1

(−2Lsθ+cθd)
2L

Rη3cϕ2

cθd
2L

R(−2Lsϕ1

sθ+cθd(sϕ1
+sϕ2

))

2L
0 | 0 | 1

,

P(q, η3) =

R²η

2/3
2Ls²
ϕ1

sθ+2Lsϕ1
sϕ2

sθ−cθds²
ϕ1

−2cθdsϕ1

sϕ2−cθds²
ϕ2

4L²
−

R²η

2/3
2Lcθs

2
ϕ1

+2Lcθsϕ1

sϕ2+ds²
ϕ1

sθ+2dsϕ1
sϕ2

sθ+ds²
ϕ2

sθ

4L²
0

Analysis of the determinant of the matrix D

det D = −

dR²η
2/3 cos ϕ1 cos ϕ2
2L

3. Control algorithms | 32

Figure 3.3: Structure of the cascade PID control

shows that singularities occur only when any HOG wheel stops rotating or the virtual shaft has no length. The length of the virtual shaft directly corresponds to the offset between the actual and desired positions during trajectory tracking. To reduce this offset, the desired trajectory hd can be constructed as

hd =

xd + d cos θdir
yd + d sin θdir
ψd
- ,

where θdir = atan2(y˙ d, ˙xd).

## 3.4 Cascade PID control

For comparison, a basic control algorithm was proposed. Cascade PID control is a widely used technique in industry for practical control tasks [ÅH95]. By skillfully transforming the problem, it becomes possible to apply well-known and simple methods for designing and tuning PID controllers. This section describes both procedures.

### 3.4.1 Algorithm

The cascade PID control, shown in Figure 3.3, consists of two feedback loops. Reference frames and symbols are identical to those used in the JPTD algorithm. In the robot’s reference frame XBYBZB, controlling each of the x, y, and θ movements is independent, so three separate controllers can be introduced for the task of tracking reference trajectories. To achieve this, the transformation matrix T θ rotates error vectors expressed in the world reference frame XWYWZW to the robot’s frame XBYBZB

T θ =

cos θ sin θ 0
− sin θ cos θ 0
0 | 0 | 1

3. Control algorithms | 33

For practical reasons, instead of transforming the errors directly, the transformation Tθ is applied to the reference values and the process values separately.
The inner feedback loop controls the velocities of the robot using the gimbal angles ϕ1, θ1, ϕ2, and θ2. The trajectory reference velocities are applied as setpoints to the PI controllers. The transformation T u, often called the “motor mixer” matrix, is derived from the robot’s kinematics, expressed in the robot’s reference frame in the following form

x˙
y˙
θ˙
- =

−Rψ˙
1 sin ϕ1 cos θ1
−Rψ˙
1 sin θ1

R

2Lψ˙
1 sin ϕ1 cos θ1 −

R

2Lψ˙
2 sin ϕ2 cos θ2

After substituting ψ˙

1 = −ψ˙

2 = ψ˙ = const and applying the small-angle approximation
sin α ≈ α
cos α ≈ 1

,

we obtain

x˙
y˙
θ˙
- =
−Rψ˙ | 0 | 0
0 | −Rψ˙ | 0
Rψ˙ 2L | 0 | Rψ˙
| | 2L

ϕ1
θ1
ϕ2
- ,

and finally

ϕ1
θ1
ϕ2
- =

−

1
Rψ˙ | 0 | 0
0 | −

1
Rψ˙ 0

1
Rψ˙ | 0 | 2L
| | Rψ˙

x˙
y˙
θ˙

The gimbal angles θ1 and θ2 control movement along the YB axis. To ensure motion without slippage, both angles must satisfy the condition θ2 = −θ1. In summary, the three controller outputs ux, uy, and uθ are merged using the formula

ϕ1
θ1
ϕ2
θ2

=

−

1
Rψ˙ | 0 | 0
0 | −
| 1
| Rψ˙ | 0

1
Rψ˙ | 0

2L
Rψ˙
0 | 1
Rψ˙ | 0

ux
uy
uθ
- = T uu.

The outer feedback loop (see Figure 3.3) controls the position of the robot by applying corrective reference velocities to the inner loop. This allows the robot’s position to converge to the reference trajectory.

### 3.4.2 Inner loop tunning

From the inner loop’s perspective, the system can be modeled as an inertial system with lag, as described in Section 2.3.3. Similarly, the model parameters K, T, and L can be obtained by applying a step input to each of the ux, uy, and uθ signals separately. To tune the internal PI controllers, the Chien-Hrones-Reswick method with

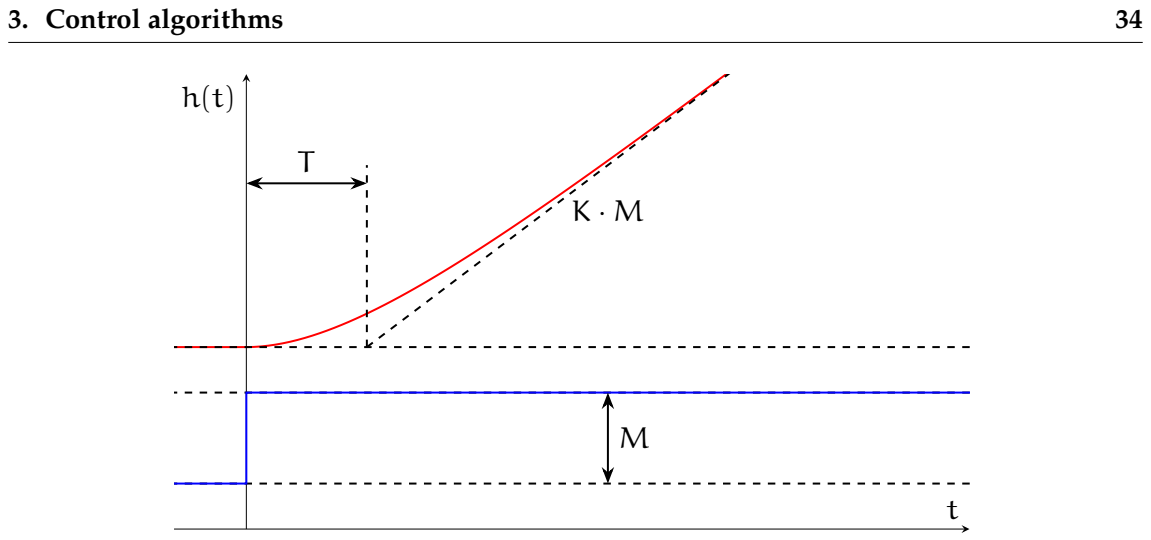
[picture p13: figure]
3. Control algorithms

Figure 3.4: Geometric properties of the step response of an integrating system

0% overshoot [ÅH95] is used, according to the formulas

Kp = 0.35 T
KL
Ki = 0.29 1
KL
Kd = 0

The results of the tuning procedure are provided in Appendix C. Using the transformation Tu, the model gain K should ideally equal 1. If K ≈ 1, it can be assumed that the step response was collected correctly.

### 3.4.3 Outer loop tunning

From the outer loop’s perspective, the system, with internal controllers running, can be modeled as an integrating system with inertia. To tune the PID controller for such a system, the λ-tuning method [ÅH95] was used. The method, shown in Figure 3.4, involves drawing additional straight lines on the step response (red plot) of an unknown integrating system to represent:

- the signal level at steady state before applying the step,
- the tangent line to the pure integrating portion of the response.

Analysis of the line’s intersection and slope reveals the system’s key geometric properties, namely, the gain K, and time constant T, which fully characterize the plant. Because the outer loop controls position by setting the reference velocity of the system, again one should expect that K equals 1 under ideal conditions. If K ≈ 1, it can be assumed that the step response was collected correctly.
The λ-tuning method consists of calculating the ideal controller C(s) using the plant transfer function P(s), and the desired closed-loop response transfer function Gz(s).

3. Control algorithms | 35

The desired step response was selected as

Gz(s) = 1 λTs + 1 ,

where λ is a user defined parameter related to the time constant of the closed-loop system. The plant was identified as

P(s) = K
s (Ts + 1)

Using the standard closed-loop transfer function of a system with error feedback

Gz(s) = C(s)P(s)
1 + C(s)P(s)
| ,

one can solve for C(s) using the formula

C(s) = 1
P(s)
| Gz(s) 1 − Gz(s) .

Finally, by grouping the coefficients of 1
s

, which defines Ki, and s, which defines Kd, the formulas for the ideal PID controller take the form
Kp = | 1 λKT

Ki = 0
Kd = | 1 λK .

# Chapter 4

# Experiments

This chapter presents the results of the experiments conducted as a part of the thesis. The robot’s geometric parameters were kept constant during all experiments, with values L = 0.13 m and R = 0.05 m. The experiments were carried out on a flat stone floor without noticeable grouting, as shown in Figure 4.1. The use of an optical sensor required selecting a floor surface with sufficiently nonuniform coloring to ensure reliable sensor readings. Furthermore, due to the use of the BEMF algorithm for BLDC motor control, all implemented control algorithms assume constant motor speeds. Motor control is handled by the internal PID controller, rather than relying on the control signals computed by the tested algorithms. For algorithms in which the control signals involve regulating servo velocity, additional integrators were introduced to compute the corresponding angle setpoints.
The reference trajectory was a variation of the Lissajous curve, as used in [Jon17], and is defined by

xd(t) = a sin
1
2

ωt

yd(t) = a cos
ωt +

π
4

θd(t) = atan2
y˙ d(t), ˙xd(t)

,

where ω =

4π
T

, T = 30 s is the period of one full loop, and a = 1 m is the trajectory span. The algorithms were also tested on various trajectory shapes, including circular, lemniscate, and linear however, the one presented above was selected for illustrative purposes. During the experiments, the trajectory tracking performance of all algorithms was evaluated for three angular velocity settings of both hemispheres: 200 rad
s

,
350 rad
s

, and 500 rad
s

. For each test, the robot’s initial position was set at the center of the room, corresponding to the origin of the world reference frame XWYWZW. At the beginning of each run, the trajectory tracking algorithm and the startup procedure for the hemisphere motors were initiated simultaneously.
The plots presented in this chapter follow a consistent format. Dotted lines represent the reference values of trajectory components and actuator setpoints. Solid lines indicate the actual control signals and the corresponding states achieved by the robot.

4. Experiments | 37

Figure 4.1: Floor in the WUST C–1 building selected for the experiments

## 4.1 Simultaneous algorithm

This section presents the results of experiments with the simultaneous algorithm (described in Section 3.1). Figures 4.2–4.7 present the results for identical control inputs applied to both hemispheres, while Figures 4.8–4.13 show the results for mirrored control inputs. The control signals were clamped‗
to the range of ±3

◦
For both variants, the results show that the robot’s orientation does not remain constant, in contrast to the simulation results reported in [Jon17]. The variant with identical control signals causes the robot to spin, as shown in Figure 4.14. On the other hand, mirrored control inputs do not significantly influence the robot’s angular velocity, since frictional torques cancel each other out, leaving only minor variations due to floor and hemisphere imperfections. The naive control law was unable to track the trajectory satisfactorily. In terms of planar movement, the robot’s behavior was consistent with the results obtained in the previously conducted simulations [Jon17]. The tracking errors ex and ey also oscillated around zero, though with greater amplitude.

## 4.2 JPTD algorithm

Next, the JPTD algorithm was applied (see Section 3.2). The results of its tests are shown in Figures 4.15–4.20. The algorithm requires special consideration regarding the reference trajectory. In this case, the reference orientation θd(t) was redefined as

θd(t) = atan2
y˙ d(t), ˙xd(t)
+

π
4

,

‗At low hemisphere speeds, the BLDC motor controllers were unable to maintain motor operation under high load conditions, which arise when the gimbals are tilted excessively. For each of the examined algorithms, similar constraints were imposed, with their values determined experimentally.

4. Experiments | 38

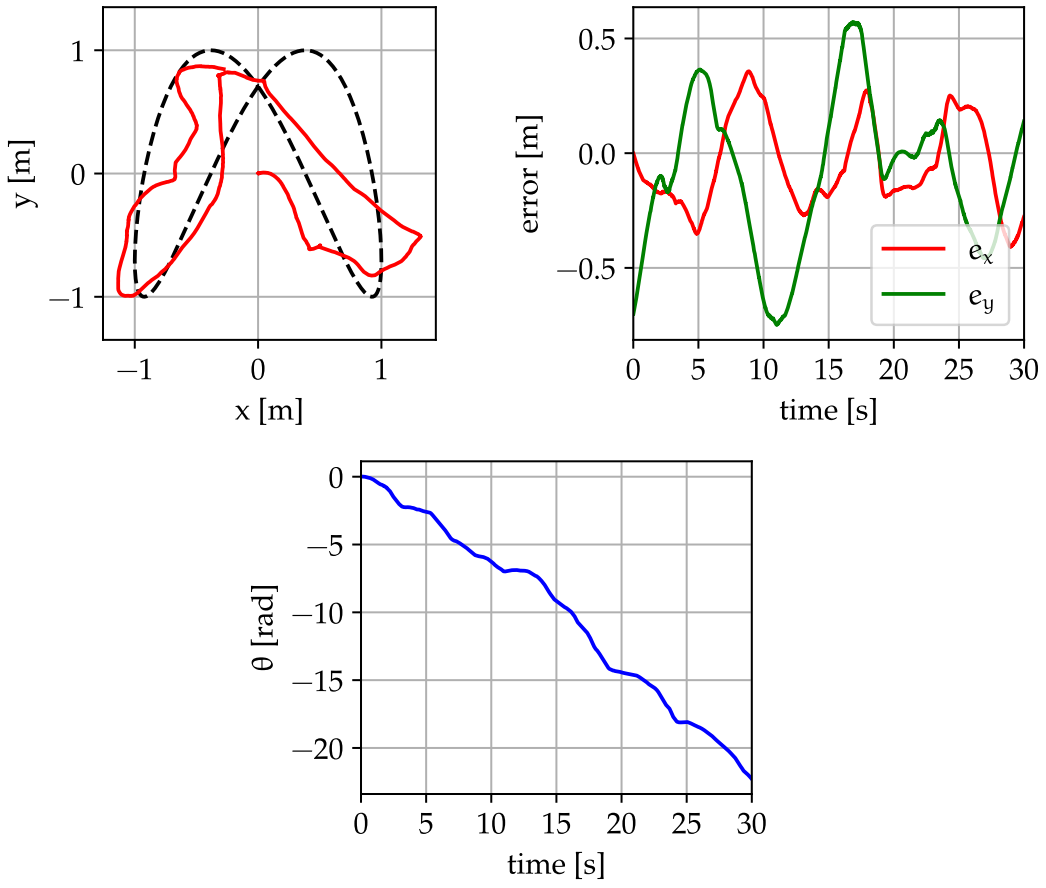
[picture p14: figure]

Figure 4.2: Results of trajectory tracking using simultaneous algorithm with identical controls for ψ˙ = -200 rad
s

, and k = 2

to avoid tracking trajectories aligned with the robot’s reference frame axes XB or YB, where the decoupling matrix becomes singular. The control signals were clamped to the range of ±4

◦
The orientation tracking performance was significantly worse than the position tracking, exhibiting noticeable offset and multiple rotations for higher hemisphere velocities, not observed in simulations [Jon17]. Unfortunately, the gain matrices K1 and K2 proposed in [Jon17] failed to ensure convergence to the desired trajectory. After increasing the gains to K1 = K2 = 200 · I, convergence in planar motion was achieved however, the robot’s orientation remained unregulated. The smallest gain values that ensured convergence across all components of the desired trajectory were determined to be 1000. As a result, the integrator blocks in the control signals saturated almost instantly, leading to chattering in the angle setpoints. Assigning higher values only to the orientation-related elements of the gain matrices leads to a decrease in overall performance.

Figure 4.3: Control inputs during trajectory tracking using simultaneous
algorithm with identical controls for ψ˙ = -200 rad

Figure 4.4: Results of trajectory tracking using simultaneous algorithm

with identical controls for ψ˙ = -350 rad

Figure 4.5: Control inputs during trajectory tracking using simultaneous
algorithm with identical controls for ψ˙ = -350 rad

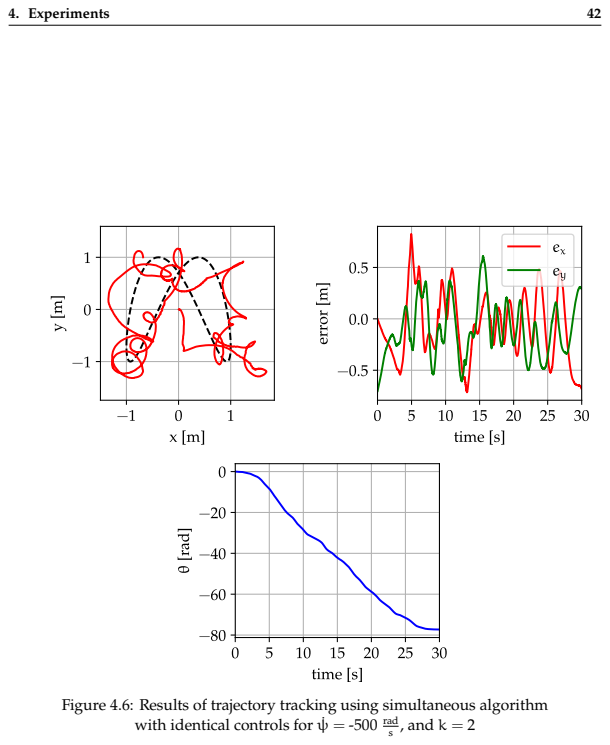
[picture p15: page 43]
4. Experiments; , and k = 2

Figure 4.6: Results of trajectory tracking using simultaneous algorithm

with identical controls for ψ˙ = -500 rad

Figure 4.7: Control inputs during trajectory tracking naive simultaneous
algorithm with identical controls for ψ˙ = -500 rad

Figure 4.8: Results of trajectory tracking using simultaneous algorithm

with mirrored controls for ψ˙ = -200 rad

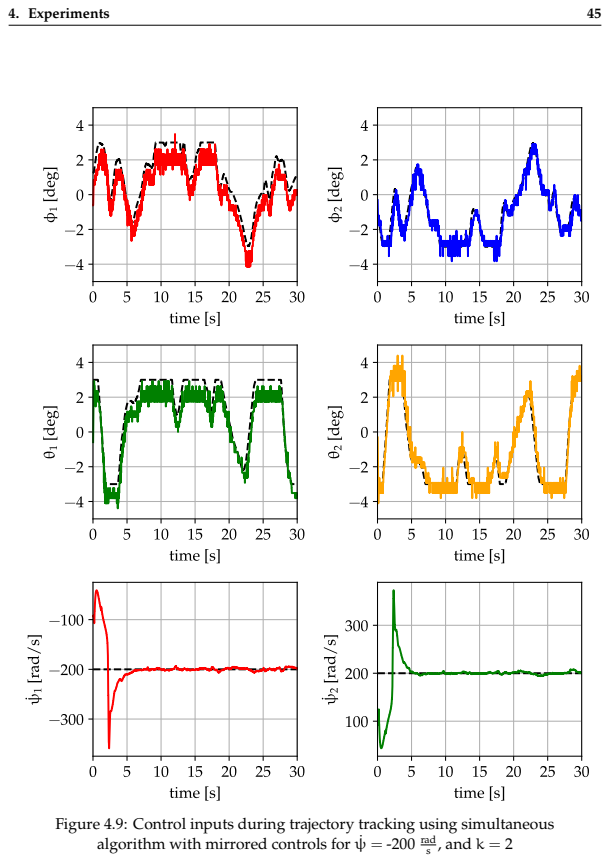
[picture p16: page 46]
4. Experiments; , and k = 2

Figure 4.9: Control inputs during trajectory tracking using simultaneous
algorithm with mirrored controls for ψ˙ = -200 rad

Figure 4.10: Results of trajectory tracking using simultaneous algorithm

with mirrored controls for ψ˙ = -350 rad

Figure 4.11: Control inputs during trajectory tracking using simultaneous

algorithm with mirrored controls for ψ˙ = -350 rad

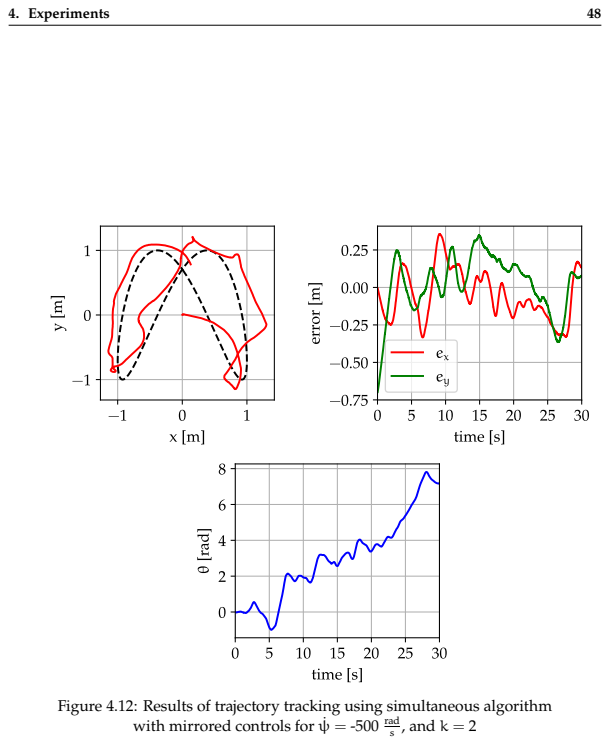
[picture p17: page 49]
4. Experiments; , and k = 2

Figure 4.12: Results of trajectory tracking using simultaneous algorithm

with mirrored controls for ψ˙ = -500 rad

Figure 4.13: Control inputs during trajectory tracking using simultaneous

algorithm with mirrored controls for ψ˙ = -500 rad

Figure 4.14: Mean robot’s angular velocity vs. hemisphere velocities

while using simultaneous algorithm

Figure 4.15: Results of trajectory tracking using JPTD algorithm
for ψ˙

Figure 4.16: Control inputs during trajectory tracking using JPTD algorithm

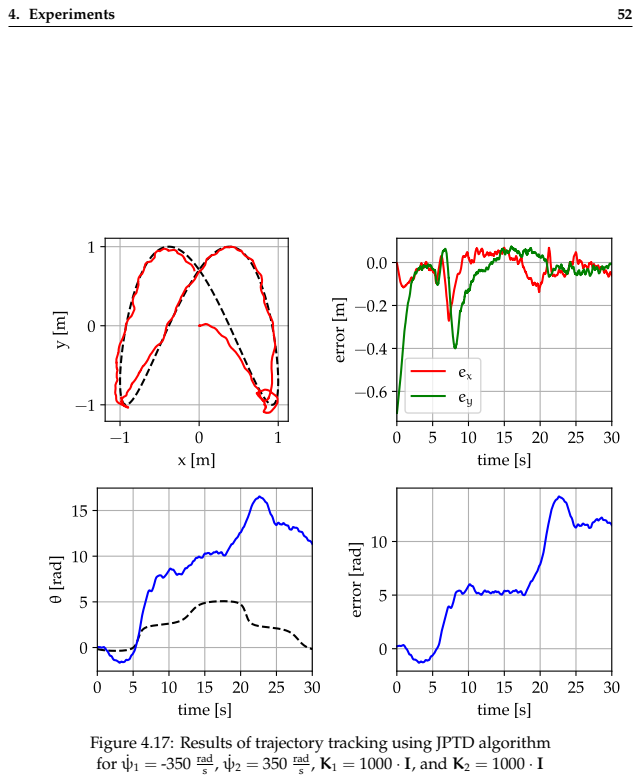
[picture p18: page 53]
4. Experiments; 1 = -350 rad s; 2 = 350 rad s; , K1 = 1000 · I, and K2 = 1000 · I

Figure 4.17: Results of trajectory tracking using JPTD algorithm
for ψ˙

Figure 4.18: Control inputs during trajectory tracking using JPTD algorithm

Figure 4.19: Results of trajectory tracking using JPTD algorithm
for ψ˙

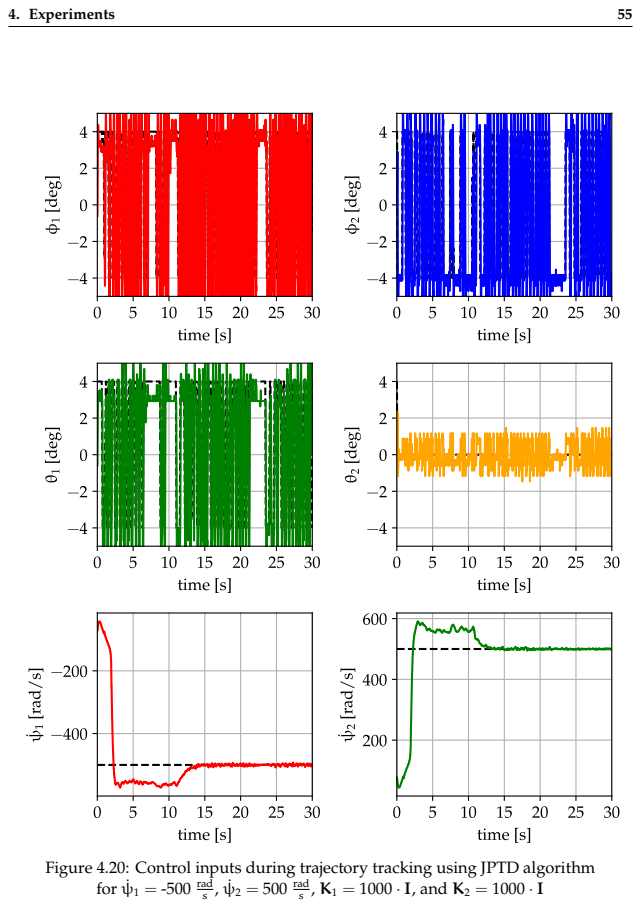
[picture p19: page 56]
4. Experiments; for ψ˙ 1 = -500 rad s; 2 = 500 rad s; , K1 = 1000 · I, and K2 = 1000 · I

Figure 4.20: Control inputs during trajectory tracking using JPTD algorithm

4. Experiments | 56

Controller Lower Bound Upper Bound
inner x | -1.5 | 1.5
inner y | -1.5 | 1.5
inner θ | -4π | 4π
outer x | -0.5 | 0.5
outer y | -0.5 | 0.5
outer θ | -π | π

Table 4.1: Antiwindup constrains used in cascade PID control

## 4.3 JPTD–1D algorithm

This section presents the results of experiments conducted using the JPTD–1D algorithm (see Section 3.3), as shown in Figures 4.21–4.26. The length of the virtual shaft was set to d = 0.1 m. The control signals were clamped to the range of ±4

◦
Due to the tracking task being defined for the virtual shaft endpoint, the robot’s position follows the trajectory accordingly, while its orientation remains uncontrolled, occasionally performing full ±360◦
rotations. The smallest values of the gain matrices K1 and K2 that ensured convergence were found to be 100 and 50, respectively. Again, the integrators saturated immediately, causing high-frequency switching of the angle setpoints between their range limits.

## 4.4 Cascade PID control

Finally, the cascade PID control strategy was applied (described in Section 3.4). The results of its tests are shown in in Figures 4.27–4.32. The tuning parameters for the inner and outer loop controllers are provided in Appendix C. The antiwindup constrains was set accordingly to the Table 4.1. The control signals were constrained to the range of ±10◦
, corresponding to the maximum allowable operating range defined by the mechanical limitations of the gimbal assembly.
The trajectory tracking performance was the best among all considered algorithms in terms of both the robot’s position and orientation, most likely due to the inclusion of basic system dynamics in the control calculations. However, during motion, the robot experienced significant oscillations along the YB axis. Nevertheless, due to the proposed transformations, the tracking performance remains unaffected by the angular velocity of the hemispheres. The ϕ2 gimbal angle undergoes the most significant variations, as it is responsible for controlling both linear motion along the XB axis and rotational motion around the ZB axis. The amplitude of the gimbal angles decreases as the hemisphere rotational speed increases.

Figure 4.21: Results of trajectory tracking using JPTD–1D algorithm
for ψ˙ = -200 rad

Figure 4.22: Control inputs during trajectory tracking using JPTD–1D algorithm

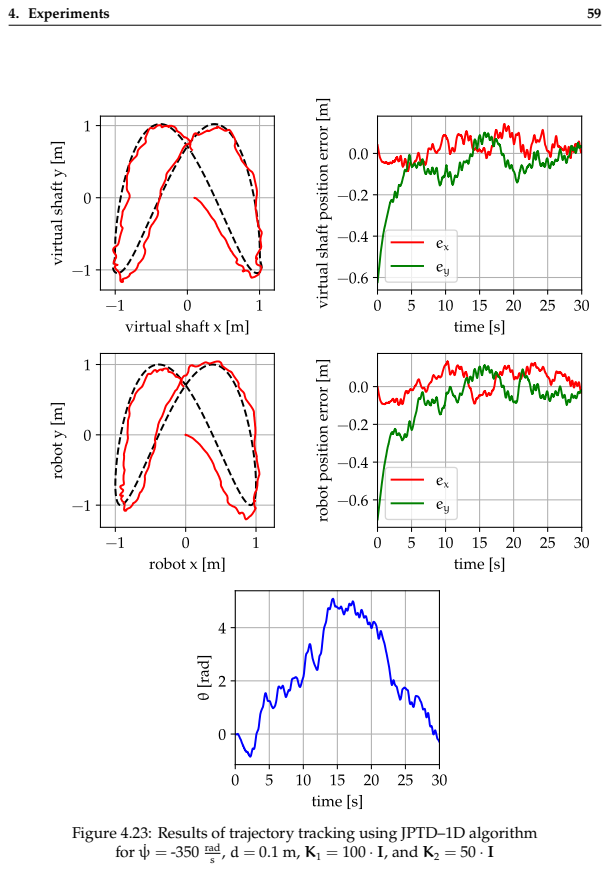
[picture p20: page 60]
4. Experiments; , d = 0.1 m, K1 = 100 · I, and K2 = 50 · I

Figure 4.23: Results of trajectory tracking using JPTD–1D algorithm
for ψ˙ = -350 rad

Figure 4.24: Control inputs during trajectory tracking using JPTD–1D algorithm

Figure 4.25: Results of trajectory tracking using JPTD–1D algorithm
for ψ˙ = -500 rad

Figure 4.26: Control inputs during trajectory tracking using JPTD–1D algorithm

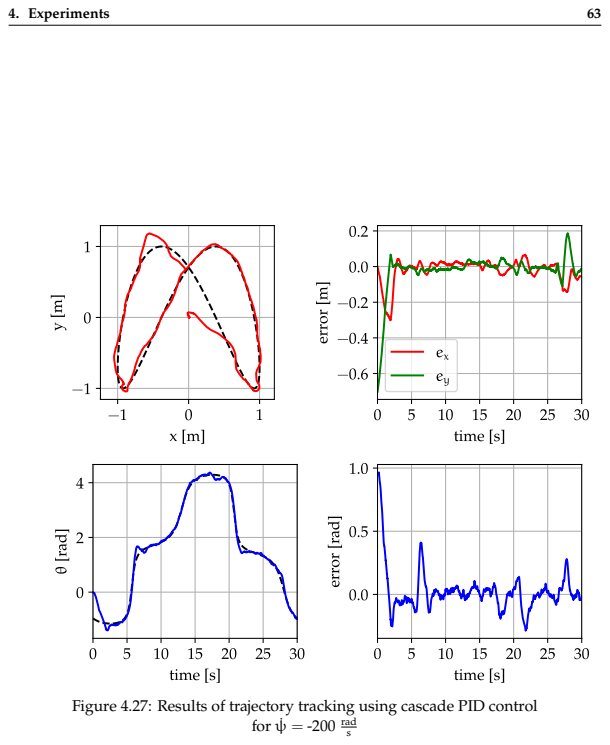
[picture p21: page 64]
4. Experiments; for ψ˙ = -200 rad s

Figure 4.27: Results of trajectory tracking using cascade PID control

Figure 4.28: Control inputs during trajectory tracking using cascade PID control

Figure 4.29: Results of trajectory tracking using cascade PID control

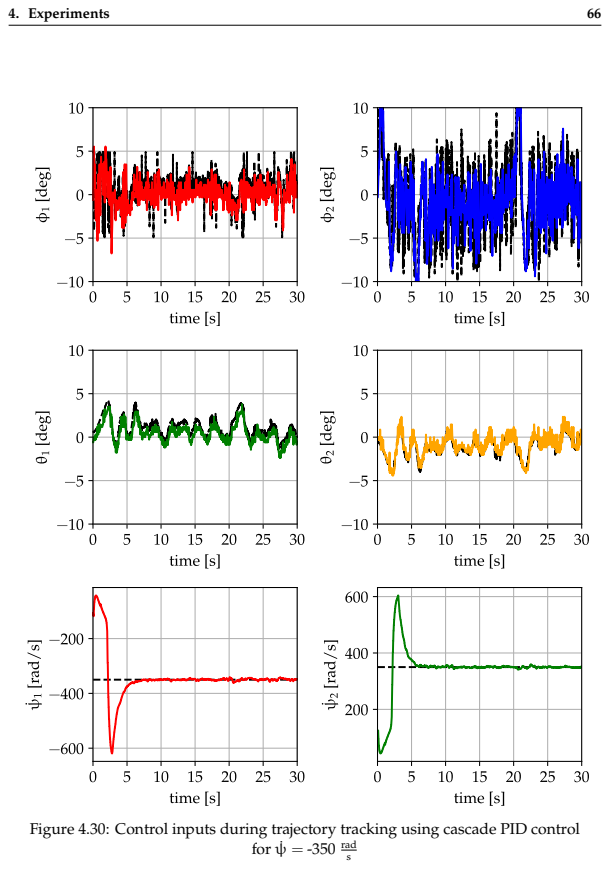
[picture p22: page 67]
4. Experiments; for ψ˙ = -350 rad s

Figure 4.30: Control inputs during trajectory tracking using cascade PID control

Figure 4.31: Results of trajectory tracking using cascade PID control

Figure 4.32: Control inputs during trajectory tracking using cascade PID control

4. Experiments | 69
Algorithm | Hemispheres Angular Velocity
200 rad
s

350 rad
s

500 rad
s
Simultaneous | XY | big oscillations | big oscillations | big oscillations
(identical) | θ | fast spin | fast spin | fast spin
Simultaneous | XY | oscillations | oscillations | oscillations
(mirrored) | θ | slow spin | slow spin | slow spin
JPTD | XY | good | good | good
| θ | constant error | not converge | not converge
JPTD–1D | XY | good | good | big oscillations
| θ | oscillations | oscillations | fast spin
Cascade PID | XY | good | good | good
| θ | good | good | good

Table 4.2: Overview of algorithms performance

## 4.5 Results overview

The results of the experiments conducted in this chapter are summarized in Table 4.2. The table presents the overall performance of the algorithms in tracking the reference position (XY) and orientation (θ) for the given hemispheres angular velocities. Among all evaluated algorithms, JPTD, JPTD–1D, and cascade PID strategy demonstrated good performance in tracking the reference position, however only the PID cascade was able to reliably control the robot’s orientation.
Unfortunately, due to environmental constraints, the true position and orientation of the robot were not recorded. Nevertheless, during numerous test runs, it was frequently observed that the estimated state deviated from the robot’s actual state, particularly during high-speed maneuvers. With increase of hemispheres angular velocity, the overall performance of control strategies relying only on the robot’s kinematics declined.

# Chapter 5

# Summary

– Otyły Panie, mam dobrą i złą wiadomość. – Zacznĳ od złej.
– Nie działa.
– Hmm, a dobra?
– Zbudowaliśmy go!
– Nareszcie!
B. Walaszek, „Kapitan Bomba – Zemsta Faraona”

The goal of this thesis was to modernize the existing mechanical design a mobile robot equipped with two HOG wheels, develop a control system for such a robot, and to utilize it for the analysis of selected trajectory tracking control algorithms. A dedicated hardware platform, including a custom controller module, was developed alongside supporting software for communication, data acquisition, sensor fusion, and the implementation of multiple control strategies. The objectives outlined in the work have been successfully achieved.
The mechanical modifications, along with the integration of new servomotors, significantly enhanced the capabilities of the platform. However, the design of the gimbal mechanism still exhibits several limitations, such as the relatively high mass of the links compared to 2 DOF spherical parallel manipulators. The overall mechanical backlash remain highly dependent on the internal servo gear quality. Vibrations occurring during operation contribute to the accelerated wear of these gears, resulting in a noticeable decrease of control precision, even by several degrees per axis. Reducing the radius of the hemispheres would improve the effective resolution of the servomotors and reduce the impact of servo backlash. Additionally, the initial assumption regarding the high rotational speed of the hemispheres proved to be incorrect. The use of a sensorless BEMF method for driving BLDC motors was found to be unsuitable for this application. Furthermore, the operational environment and the maximum velocity of the robot were significantly constrained by the use of an optical flow sensor, which is primarily intended for far-field applications. Relying solely on velocity integration for position estimation, without any external correction mechanisms, resulted in considerable position drift, particularly evident during high-speed motion. In the future, alternative methods for robot localization need to be introduced.
The analysis of the experiments indicates that control strategies based solely on the robot’s kinematics exhibit poor performance in practical applications. The cascade PID control, being the only algorithm that incorporates the basic robot’s dynamics, achieved the best results. As the angular velocities of the hemispheres increased, the tracking performance of the kinematic controllers decreased. The two tested variants of the simultaneous control strategy demonstrated that the friction between the hemispheres and even a flat ground surface is not negligible. To minimize the influence of this friction, the hemispheres should rotate in opposite directions at equal speeds. One of

5. Summary | 71

Figure 5.1: Hyperloop One magnetic levitation test platform (2017) [Mul]

the conclusions from [Jon17] remain valid: in the future, the dynamic model of the Hogger²
robot needs to be derived and utilized for the design of control system. It is necessary to develop a physics simulation for testing upcoming control algorithms that includes system dynamics, hemisphere and ground irregularities, as well as friction, using modern frameworks like MuJoCo [TET12], NVIDIA Isaac [LMH⁺18], or even Drake [TtDDT19].
The most significant drawback of the HOG drive is the unrealistic assumption of a single point of contact between the hemisphere and the ground. Even small shape imperfections cause noticeable movement errors. During operation, the hemispheres wear unevenly near the rotation axis, which is critical when combined with above. If the center of gravity were placed below the geometric center of the hemispheres, it would be possible to eliminate the additional support wheel, creating a self-stabilizing system with only two points of contact. Taking this idea further, it might even be feasible to transform the Hogger²
robot into an amphibious vehicle, provided that the hemispheres are sufficiently buoyant and the center of buoyant force is located above the center of gravity.
It is worth mentioning that there exist magnetic levitation methods [CBK19], which use rotating discs populated with high-strength magnets above copper rails, as shown in Figure 5.1. By applying rotational motion, the magnets generate a magnetic field that acts as an electromagnetic suspension, eliminating friction caused by surface contact. In the future, replacing the hemisphere wheels with a form of magnetic levitation may eliminate issues related to friction and surface irregularities of the hemispheres. An asymmetrical magnetic field generated by magnets rotating around a gimballed axis may be the next evolution stage of the HOG wheel.

# Bibliography

[Ack] | E. Ackerman. | You’ve Never Seen a Robot Drive System Like This
Before. https://spectrum.ieee.org/youve-never-seen-a-drive-systemlike-this-before. (https://spectrum.ieee.org/youve-never-seen-a-drive-system-like-this-before)
[ÅH95] K. J. Åström and T. Hägglund. PID Controllers. Setting the standard for automation. International Society for Measurement and Control, 1995.

[Boc19] J. Boczar. Control system for two HOG wheel mobile robot. Master’s thesis, https://kcir.pwr.edu.pl/~mucha/Pracki/Jedrzej_Boczar_praca_magisterska.pdf, (https://kcir.pwr.edu.pl/~mucha/Pracki/Jedrzej_Boczar_praca_magisterska.pdf) Wrocław University of Science and Technology, 2019.

[CBK19] E. Chaidez, Shankar P. Bhattacharyya, and Adonios N. Karpetis. Levitation Methods for Use in the Hyperloop High-Speed Transportation System. Energies, 12(21), 2019.

[Cha] | J. P. Charras. KiCad. https://www.kicad.org/.
[DER] | DERUTU Inc. DERUTU Basement polishing robot. https://www.youtube.
com/watch?v=O5tWiZWLNQU. (https://www.youtube.com/watch?v=O5tWiZWLNQU)
[Fur] | S. Furuhashi. MessagePack. https://msgpack.org/index.html.
[Gór17] | D. Góral. Konstrukcja robota mobilnego napędzanego dwiema półs-
ferami. | Bachelor’s thesis, https://kcir.pwr.edu.pl/~mucha/Pracki/
Damian_Goral_praca_inzynierska.pdf, (https://kcir.pwr.edu.pl/~mucha/Pracki/Damian_Goral_praca_inzynierska.pdf) Wrocław University of Science and Technology, 2017. (in Polish).
[Gro] | Qt Group. Qt. https://www.qt.io/.
[Gun] | C. Gunyon. An implementation of the MessagePack serialization format in
C. https://github.com/camgunz/cmp. [Hon] Honeywell. Three-Axis Digital Compass IC HMC5883L. https://www.farnell.com/datasheets/1683374.pdf.
[ifd] | ifdesign.com. | Basement Concrete Troweling and Leveling Robot.
https://ifdesign.com/en/winner-ranking/project/basement-concretetroweling-and-leveling-robot/314447. (https://ifdesign.com/en/winner-ranking/project/basement-concrete-troweling-and-leveling-robot/314447)
[Inf] | Infineon. | OptiMOS-T2 Power-Transistor. | https://www.infineon.
com/dgdl/Infineon-IPD90N04S4L_04-DS-v01_00-en.pdf?fileId= db3a304328c6bd5c01291cab92685eaa. (https://www.infineon.com/dgdl/Infineon-IPD90N04S4L_04-DS-v01_00-en.pdf?fileId=db3a304328c6bd5c01291cab92685eaa)

Bibliography | 73
[Ins] | Texas Instruments. | LM2105 107-V, 0.5-A, 0.8-A Half-Bridge
Driver with 5-V UVLO and Integrated Bootstrap Diode. | https:
//www.ti.com/lit/ds/symlink/lm2105.pdf?ts=1683842340255&ref_url= https%253A%252F%252Fwww.ti.com%252Fproduct%252FLM2105. (https://www.ti.com/lit/ds/symlink/lm2105.pdf?ts=1683842340255)
[Inv] | InvenSense. | MPU-6000 and MPU-6050 Product Specification Revi-
sion 3.4. | https://invensense.tdk.com/wp-content/uploads/2015/02/
MPU-6000-Datasheet1.pdf. (https://invensense.tdk.com/wp-content/uploads/2015/02/MPU-6000-Datasheet1.pdf)
[Jac21] E. B. Jacobsen. Modelling and Control of Thrust Vectoring Mono-copter. Master’s thesis, https://projekter.aau.dk/projekter/files/421577367/Master_Thesis_Emil_Jacobsen_v5.pdf, (https://projekter.aau.dk/projekter/files/421577367/Master_Thesis_Emil_Jacobsen_v5.pdf) Aalborg University, 2021.
[JG] | B. Jacob and G. Guennebaud. Eigen. https://eigen.tuxfamily.org/index.
php?title=Main_Page. (https://eigen.tuxfamily.org/index.php?title=Main_Page)
[Jon14] | P. Joniak. | Badania symulacyjne zachowania robota mobilnego
napędzanego dwiema półsferami. | Bachelor’s thesis, https://kcir.
pwr.edu.pl/~mucha/Pracki/Pawel_Joniak_projekt_inzynierski.pdf, (https://kcir.pwr.edu.pl/~mucha/Pracki/Pawel_Joniak_projekt_inzynierski.pdf) Wrocław University of Science and Technology, 2014. (in Polish).

[Jon17] P. Joniak. Zadanie sterowania robota mobilnego napędzanego dwiema półsferami. Master’s thesis, https://kcir.pwr.edu.pl/~mucha/Pracki/Pawel_Joniak_praca_magisterska.pdf, (https://kcir.pwr.edu.pl/~mucha/Pracki/Pawel_Joniak_praca_magisterska.pdf) Wrocław University of Science and Technology, 2017. (in Polish).

[KAV] KAVAN. C2830-750. https://kavanrc.com/en/item/kavan-brushlessmotor-c2830-750-140796. (https://kavanrc.com/en/item/kavan-brushless-motor-c2830-750-140796)
[KCB⁺23] M. Kabiri, C. Cimarelli, H. Bavle, J. L. Sanchez-Lopez, and H. Voos. A Review of Radio Frequency Based Localisation for Aerial and Ground Robots with 5G Future Perspectives. Sensors, 23(1), 2023.
[KSBT⁺17] J. Krishnaraj, K. Sangeetha, M. V. Babu Tanneru, V. V. S. Prasad Harnadh, and M. Vishnu Vardhan. A Mecanum Wheel Based Robot Platform for Warehouse Automation. International Journal of Mechanical Engineering and Technology, 8:181–189, 07 2017.
[LCA] | A. Lita, M. Cheles, and A. Abacan. | Sensorless BLDC Con-
trol with Back-EMF Filtering Using a Majority Function. | https:
//ww1.microchip.com/downloads/aemDocuments/documents/MCU16/ ApplicationNotes/ApplicationNotes/AN1160-Sensorless-BLDC-Controlwith-Back-EMF-Filtering-Using-a-Majority-Function-DS00001160.pdf. (https://ww1.microchip.com/downloads/aemDocuments/documents/MCU16/ApplicationNotes/ApplicationNotes/AN1160-Sensorless-BLDC-Control-with-Back-EMF-Filtering-Usin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) [LMH⁺18] J. Liang, V. Makoviychuk, A. Handa, N. Chentanez, M. Macklin, and D. Fox. GPU-Accelerated Robotic Simulation for Distributed Reinforcement Learning, 2018.
[Lub23] T. Lubelski. Budowa małego mobilnego robota laboratoryjnego klasy (1,2). Bachelor’s thesis, https://kcir.pwr.edu.pl/~mucha/Pracki/Tomek_Lubelski_praca_inzynierska.pdf, (https://kcir.pwr.edu.pl/~mucha/Pracki/Tomek_Lubelski_praca_inzynierska.pdf) Wrocław University of Science and Technology, 2023. (in Polish).

Bibliography | 74
[mec38] | Hemisphere Drive Speedster. | Mechanics and Handicraft, | 5(9),
1938. | https://web.archive.org/web/20201201092333/http://blog.
modernmechanix.com/hemisphere-drive-speedster/#more. (https://web.archive.org/web/20201201092333/http://blog.modernmechanix.com/hemisphere-drive-speedster/)
[Moż24] E. Możdżeń. Controller for Hogger² HOG wheel robot – project proposal. Report, https://github.com/Eryk-Mozdzen/hogger2/blob/master/docs/intermediate_project_report_1.pdf, (https://github.com/Eryk-Mozdzen/hogger2/blob/master/docs/intermediate_project_report_1.pdf) Wrocław University of Science and Technology, 2024.
[Moż25] | E. Możdżeń. | Controller for Hogger² HOG wheel robot – final re-
port. Report, https://github.com/Eryk-Mozdzen/hogger2/blob/master/docs/intermediate_project_report_final.pdf, (https://github.com/Eryk-Mozdzen/hogger2/blob/master/docs/intermediate_project_report_final.pdf) Wrocław University of Science and Technology, 2025.

[Mul] D. Muller. Electromagnetic Levitation Quadcopter. https://www.youtube.com/watch?v=pCON4zfMzjU. (https://www.youtube.com/watch?v=pCON4zfMzjU)
[Ozy] T. Ozyagcilar. Calibrating an eCompass in the Presence of Hard- and Soft-Iron Interference. https://www.nxp.com/docs/en/application-note/AN4246.pdf. (https://www.nxp.com/docs/en/application-note/AN4246.pdf)
[Pix] | PixArt | Imaging | Inc. | PMW3901MB-TXQT: | Optical | Motion
Tracking | Chip. | https://wiki.bitcraze.io/_media/projects:
crazyflie2:expansionboards:pot0189-pmw3901mb-txqt-ds-r1.00-200317_20170331160807_public.pdf. (https://wiki.bitcraze.io/_media/projects:crazyflie2:expansionboards:pot0189-pmw3901mb-txqt-ds-r1.00-200317_20170331160807_public.pdf)
[ROBa] ROBOBLOCK. AI Concrete Slab Finisher Robot. https://www.youtube.com/watch?v=kyBuMxqpy-o. (https://www.youtube.com/watch?v=kyBuMxqpy-o)
[ROBb] ROBOTICS. Dynamixel AX-12A eManual. https://emanual.robotis.com/docs/en/dxl/ax/ax-12a/. (https://emanual.robotis.com/docs/en/dxl/ax/ax-12a/)
[Ryb13] | M. Rybczyński. Model robota mobilnego napędzanego za pośrednictwem
półsfery. | Bachelor’s thesis, https://kcir.pwr.edu.pl/~mucha/Pracki/
Michal_Rybczynski_praca_inzynierska.pdf, (https://kcir.pwr.edu.pl/~mucha/Pracki/Michal_Rybczynski_praca_inzynierska.pdf) Wrocław University of Science and Technology, 2013. (in Polish).

[STM] STMicroelectronics. RM0481 Reference manual. https://www.st.com/resource/en/reference_manual/rm0481-stm32h52333xx-stm32h56263xxand-stm32h573xx-armbased-32bit-mcus-stmicroelectronics.pdf. (https://www.st.com/resource/en/reference_manual/rm0481-stm32h52333xx-stm32h56263xx-and-stm32h573xx-armbased-32bit-mcus-stmicroelectronics.pdf) [TET12] E. Todorov, T. Erez, and Y. Tassa. MuJoCo: A physics engine for model-based control. In 2012 IEEE/RSJ International Conference on Intelligent Robots and Systems, pages 5026–5033, 2012.
[TM17] K. Tchoń and R.Muszyński. MathematicalMethods of Automation and Robotics.
2017. https://kcir.pwr.edu.pl/~mucha/Skrypty/KTRM_MMAiR_eng.pdf. [TtDDT19] R. Tedrake and the Drake Development Team. Drake: Model-based design and verification for robotics. https://drake.mit.edu, 2019.

[Wika] Wikipedia. Extended Kalman filter. https://en.wikipedia.org/wiki/Extended_Kalman_filter. (https://en.wikipedia.org/wiki/Extended_Kalman_filter)

Bibliography | 75
[Wikb] | Wikipedia. JSON. https://en.wikipedia.org/wiki/JSON.
[Wikc] | Wikipedia. Singular value decomposition. https://en.wikipedia.org/
wiki/Singular_value_decomposition. (https://en.wikipedia.org/wiki/Singular_value_decomposition)
[zer] | ZeroMQ. https://zeromq.org/.

# Appendix A

# Electronic schematic

This appendix contains the electronic schematics and PCB images of the controller module‗
. The design was created using the KiCad software [Cha].

‗The complete hardware design, firmware source code, code generation tools, endpoint applications, and supporting utilities, along with previously unpublished materials provided by the authors of [Jon14, Jon17, Boc19], are available in a public Git repository https://github.com/Eryk-Mozdzen/hogger2.

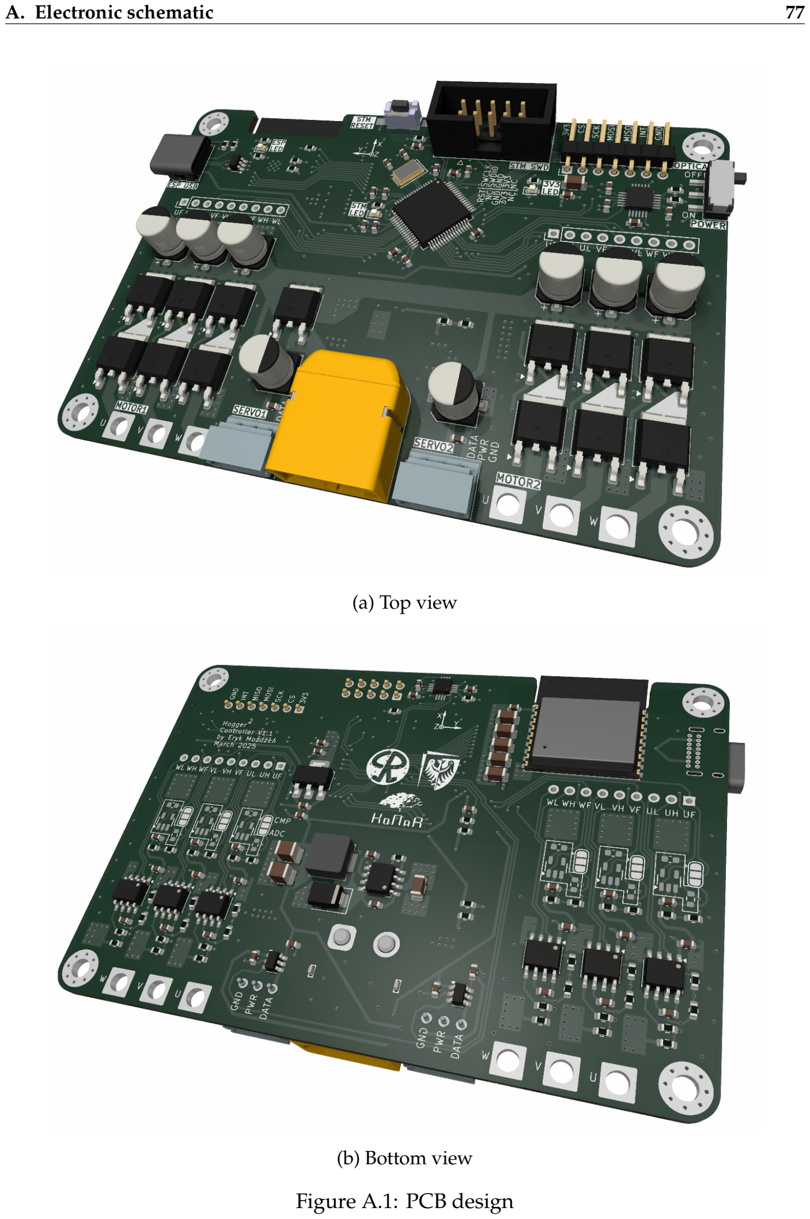
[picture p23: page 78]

A. Electronic schematic | 77
(a) Top view
(b) Bottom view

Figure A.1: PCB design

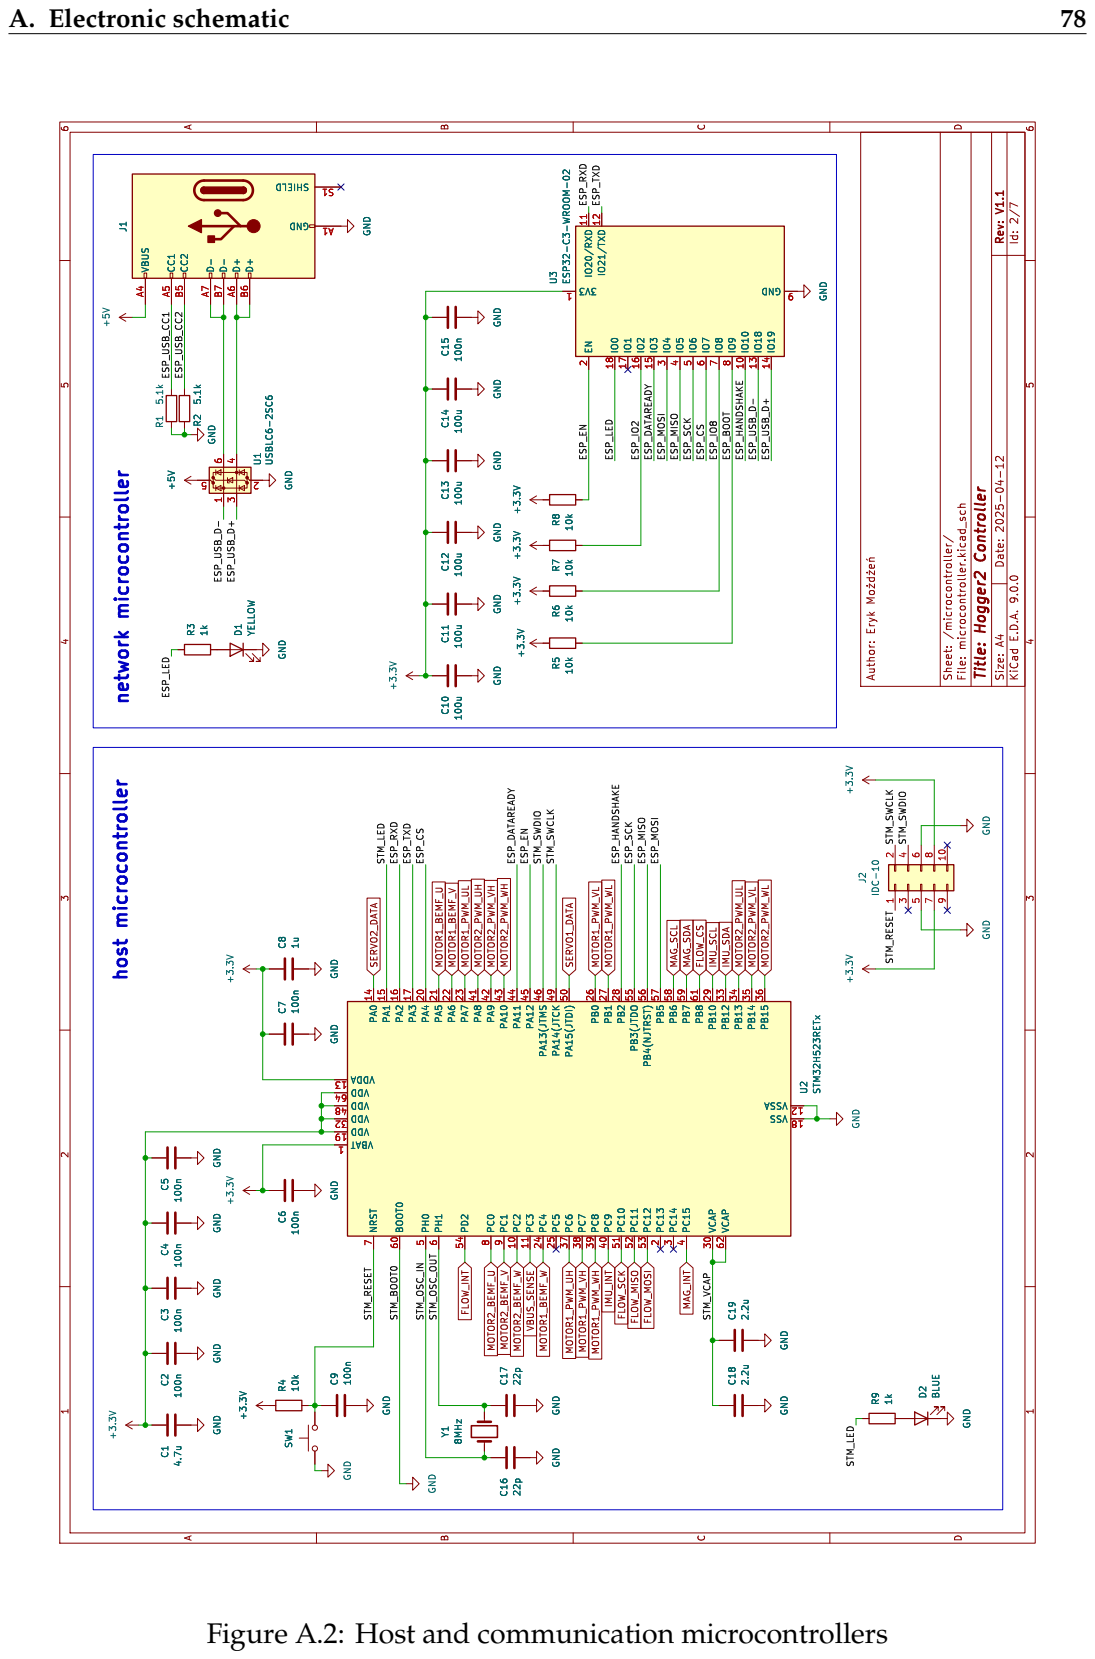
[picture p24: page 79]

D Date: 2025-04-12 KiCad E.D.A. 9.0.0 Rev: V1.1 Size: A4

J1 SHIELD S1 GND A1 VBUS A4 CC1 A5 CC2 B5 D- A7 D- B7 D+ A6 D+ B6 GND

Id: 2/7 Title: Hogger2 Controller File: microcontroller.kicad_sch Sheet: /microcontroller/ Author: Eryk þÿMo|d|eD

ESP_USB_CC2 ESP_EN network microcontroller host microcontroller

+3.3V GND +3.3V NRST 7 BOOT0 60 PH0 5 PH1 6 PD2 54 PC0 8 PC1 9 PC2 10 PC3 11 PC4 24 PC5 25 PC6 37 PC7 38 PC8 39 PC9 40 PC10 51 PC11 52 PC12 53 PC13 2 PC14 3 PC15 4 VCAP 30 VCAP 62 VBAT

U2STM32H523RETx NRST 7 BOOT0 60 PH0 5 PH1 6 PD2 54 PC0 8 PC1 9 PC2 10 PC3 11 PC4 24 PC5 25 PC6 37 PC7 38 PC8 39 PC9 40 PC10 51 PC11 52 PC12 53 PC13 2 PC14 3 PC15 4 VCAP 30 VCAP 62 VBAT

Figure A.2: Host and communication microcontrollers

D Date: 2025-03-09 KiCad E.D.A. 9.0.0 Rev: V1.1 Size: A4

Id: 3/7 Title: Hogger2 Controller File: power.kicad_sch Sheet: /power/ Author: Eryk þÿMo|d|eD

should be 0.75V VBUS voltage

LV14340 VIN 2 EN 3 RT/SYNC 4 SS 6 GND

J3 XT-60 VIN 2 EN 3 RT/SYNC 4 SS 6 GND

D Date: 2025-03-09 KiCad E.D.A. 9.0.0 Rev: V1.1 Size: A4

Id: 4/7 Title: Hogger2 Controller File: sensors.kicad_sch Sheet: /sensors/ Author: Eryk þÿMo|d|eD

connected to external PMW3901 dev-board accelerometer

10u/50V SDA 24 SCL 23 AD0 9 FSYNC 11 CLKIN 1 VLOGIC

INT 12 AUX_DA 6 AUX_CL 7 CPOUT 20 REGOUT 10 U6 MPU-6050 C34

INT 12 AUX_DA 6 AUX_CL 7 CPOUT 20 REGOUT 10 U7 HMC5883L SETP 8 SETC 12 C1 10 VDDIO 13 S1

U6 MPU-6050 SDA 24 SCL 23 AD0 9 FSYNC 11 CLKIN 1 VLOGIC

D Date: 2025-03-09 KiCad E.D.A. 9.0.0 Rev: V1.1 Size: A4

Id: 7/7 Title: Hogger2 Controller File: motor1.kicad_sch Sheet: /motor1/ Author: Eryk þÿMo|d|eD

100n GND Figure A.5: Motor 1 control circuits

MOTOR 1 triple half-bridge

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

Id: 7/7 Title: Hogger2 Controller File: motor2.kicad_sch Sheet: /motor2/ Author: Eryk þÿMo|d|eD

PHASE_V MOTOR 2 triple half-bridge MOTOR 2 BEMF signals

Figure A.6: Motor 2 control circuits

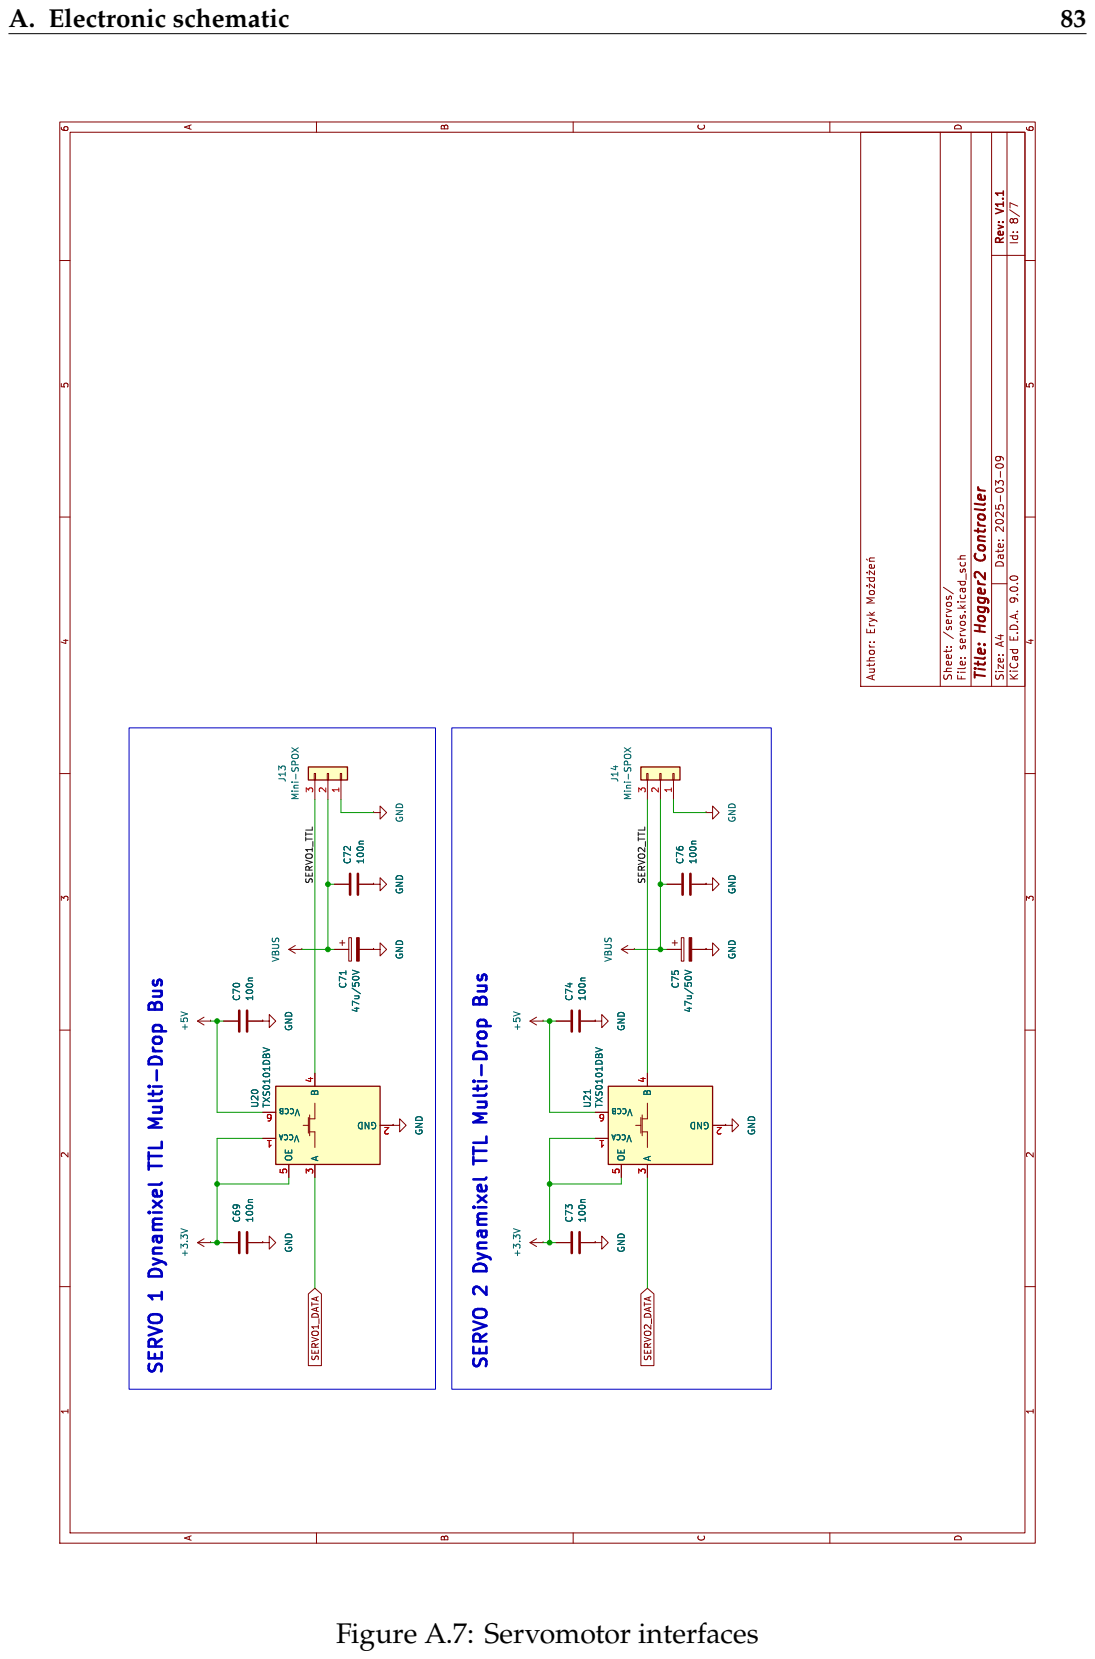
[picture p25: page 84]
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

Id: 8/7 Title: Hogger2 Controller File: servos.kicad_sch Sheet: /servos/ Author: Eryk þÿMo|d|eD

100n GND GND GND GND

SERVO1_TTL SERVO2_TTL SERVO 2 Dynamixel TTL Multi-Drop Bus

SERVO 1 Dynamixel TTL Multi-Drop Bus

# Appendix B

# Motor controller tunning

This appendix contains the results of motor step response analysis as well as PID controller parameters obtained from CHR 20% method [ÅH95]. The Table B.1 contains best-fit 4-parameter model values to the step responses collected from motors with wheels attached running in the air (no load conditions), geometry parameters and final controller settings. Data samples as well as tangent lines are shown in Figures B.1 and B.2.

Parameter Motor 1 Motor 2

model

Km | 1260 | 1200
T1m | 0.227 | 0.0614
T2m | 0.227 | 0.396
Lm | 0.00870 | 0.0395

geometry

K | 1260 | 1200
T | 0.616 | 0.557
L | 0.0726 | 0.0749

controller

Kp | 0.00643 | 0.00590
Ki | 0.00745 | 0.00756
Kd | 0.000219 0.000208

Table B.1: Motors tunning parameters

Figure B.1: Step response of motor 1

Figure B.2: Step response of motor 2

# Appendix C

# Cascade PID tunning

This appendix presents the results of the robot’s step response analysis, along with the PID controller parameters obtained using the CHR 0% overshoot method and the λ-tuning method [ÅH95]. The Table C.1 contains best-fit 4-parameter based on step responses of the robot’s velocities during inner loop tuning, along with geometric parameters and the final inner controller settings. Table C.2 presents the geometric characteristics extracted from step responses of the robot’s positions during outer loop tuning, together with the final outer controller settings. Step response plots for the inner system are shown in Figures C.1, C.2, and C.3, while the outer system responses are shown in Figures C.4, C.5, and C.6. All step response experiments were conducted with a fixed value of ψ˙ = −250 rad
s

Parameter Controller x Controller y Controller θ

model

| Km | 1.59 | 0.980 | 1.20
| T1m | 0.00136 | 0.147 | 0.114
| T2m | 0.514 | 0.147 | 0.295
| Lm | 0.0296 | 0.133 | 0.0203
geometry | K | 1.59 | 0.980 | 1.20
| T | 0.522 | 0.399 | 0.537
| L | 0.0426 | 0.175 | 0.0689
controller | Kp | 3.73 | 0.816 | 2.26
| Ki | 5.95 | 1.70 | 3.51

Table C.1: Inner loop tuning parameters

Parameter | Controller x Controller y Controller θ
geometry | K | 0.905 | 0.932 | 1.04
| T | 0.259 | 0.296 | 0.339
controller | λ | 1 | 1 | 0.25
| Kp | 4.26 | 3.63 | 11.3
| Kd | 1.10 | 1.07 | 3.84

Table C.2: Outer loop tuning parameters

Figure C.1: Step response of inner system in x axis

Figure C.2: Step response of inner system in y axis

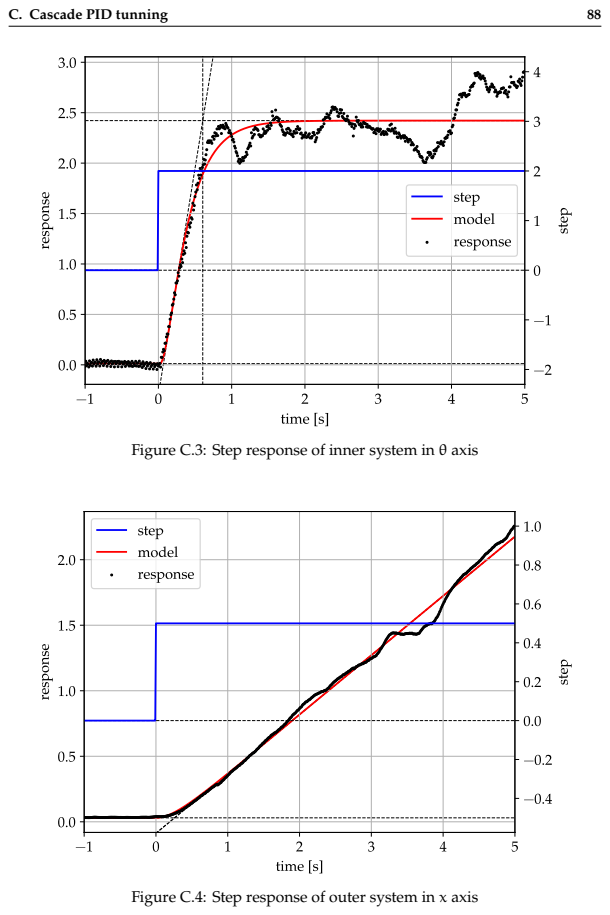
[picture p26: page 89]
C. Cascade PID tunning

Figure C.3: Step response of inner system in θ axis

Figure C.4: Step response of outer system in x axis

Figure C.5: Step response of outer system in y axis

Figure C.6: Step response of outer system in θ axis

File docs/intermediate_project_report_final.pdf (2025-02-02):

## Final report Controller for Hogger² HOG wheel robot

Eryk Możdżeń

January 27, 2025

## 1 Intro and goals

Hogger²
is a mobile robot with two HOG (Hemispherical Omnidirectional Gimbaled) (https://en.wikipedia.org/wiki/Hemispherical_omnidirectional_gimbaled_wheel) wheels belonging to KCiR. In the past, many diploma theses have been written on modeling and controlling a robot with such a drive [9], but none of them have tested them on a real robot, among other things due to the lack of efficient hardware.
The outcome of the project will be a robot with implemented simple algorithm for movement without slippage on the flat ground. The robot should be controlled wirelessly from PC.

## 2 Completed tasks

### 2.1 Hardware controller design

Hardware design of version 1.0 (first one) of the controller board was developed using KiCad [2]. Hardware should fulfill requirements shown on picture 1. The most important features are:

- two 3-phase inverters capable of controlling BLDC motors with sensorless method
- four PWM signals with appropriate voltages that allows controlling standard servos
- on–board MEMS accelerometer and gyroscope and support for external optical sensor
- wireless communication capabilities

Comparison between design and final working circuit and custom casing is available in picture 2.
After manual assembly, the MOSFET transistors driving the BLDC coils were found to burn out con-stantly. In order to fix this issue I added additional resistors, visible in picture 2b. Of course, some traces also need small fixes due to not using ERC (Electrical Rule Checker) during the development phase. From this reason some small wire is visible in picture 2d.
As on–board MEMS IMU chip MPU6050 was selected due to simplicity, cost and proven reliability in previous robotics projects. It consist of 3–axis accelerometer and 3–axis gyroscope that will be very helpful for estimating pose of the robot on the ground in near future. Additionally external optical sensor PMW3901 was added to obtain direct measurements of velocity of the robot in X and Y direction.
In previous thesis in field of mobile robots [10] network interface were used to communicate with the robot. As a continuation of this idea I decided to use ESP32C3 microcontroller as a slave device connected to the main unit. To handle potential electromagnetic interference from MOSFETs and motors, a backup radio module (nRF24L01+) was included. The fears turned out to be unfounded, the ESP32 RF interface performed very well even near working motors. It turns out that most problematic are servos, which generates current spikes capable of reset the ESP. Solution was to solder additional bulk capacitors (5x 100uF) ”in the air” to power pads of the ESP32, also visible in picture 2b.
Enclosure was designed using claud CAD platform Onshape [12] and then 3D–printed from PLA. Mounting holes ware design to match existing mount points on the robot’s frame.


Figure 1: Electronic architecture

### 2.2 BLDC motor velocity control

In the task of controlling HOG–wheeled mobile robot wheels must spin at relatively high speeds. From this reason sensorless method was chosen to control BLDC motor without need of additional sensors mounted on each motor, like encoders or hall sensors. In short, the six step algorithm consists of 6 different motor commutations (one phase is connected to ground, one to supply voltage and is floating) are driven one after another in specific order. In each commutation floating phase is inducing voltage due to back electromotive force (BEMF) while rotor spin. Shape of this voltage should be similar to trapezoidal wave, while zero–cross point (ZC) should be in the middle of each commutatation to obtain maximum torque (using this method). To obtain stable angular velocity of the rotor, PI controller control PWM duty cycle (related with motor torque) of powered phases in each commutation. In order to detect ZC event external hardware comparators were used. Side effect of this algorithm is knowledge about rotor angular velocity that can be used in sensor fusion as odometry input in the future.
To obtain sufficient BEMF amplitude, startup procedure is needed to ramp up motor velocity (open–loop) at the begin. After that smooth transition between open–loop and closed–loop was needed.
Results of voltage phases as well as comparator output is shown on picture 3. In the middle of each tON of PWM signal comparator is sampled. To reject jitter near ZC, software filter was implemented. During tests presented algorithm proofs that can drive BL2215/25 motor (without load) up to theoretical maximum (950 KV · 12.4 V ≈ 1232 rad
s

), so it can be considered that algorithm is implemented well. Test on the ground using two PropDrive 28–30 (750 KV) motors showed, that robot is able to spin the motors under load sufficient for movement. After tilting hemisphere too much, rotor stops in place and startup procedure need to be fired once again. In order to improve performance and remove high frequency noise, audible for humans, PWM frequency was setup to 50kHz.

### 2.3 Servo control

Currently, robot’s frame uses standard old avionic servos that are powered directly from 5V. Control comes directly from the microcontroller in form of PWM signal, with frequency 50Hz and duty cycle from 1ms (-90◦

) to 2ms (+90◦
). Each of servos have its own offset due to not perfect gimbal mechanism, so additional calibration on station app site was needed. Future iterations may use servos with reduced gearbox backlash and feedback capabilities.

### 2.4 Reading on–board sensors

Presented version of the controller contain IMU chip MPU6050 [8] (integrated 3–axis accelerometer and 3–axis gyroscope) and support for external optical flow sensor PMW3901 [7]. Scope of this project focus on


(a) front render | (b) front physical
(c) back render | (d) back physical
(e) enclosure render | (f) enclosure physical

Figure 2: Comparison between design and physical realization


Figure 3: Motor phase voltage (yellow) and comparator output (blue) during closed–loop operation

reading measurements from those sensors continuously and converting them to physical units. For IMU I²C peripheral was used with DMA (Direct Memory Access) to offload microcontroller core, interrupt configure as ”data ready” trigger sensor readout on around 1kHz. For optic feedback SPI interface is periodically samples on 50Hz. Data from both sensors are converted from bytes to floating point values in SI units. In the future probably additional magnetometer chip will be places on the board to improve sensor fusion results.

### 2.5 Wireless communication

Selected host microcontroller STM32U5 [11] does not support wireless communication. Originally, there was two ides to resolve this issue. First of them was placing ESP32C3 [3] as a wireless network interface, this should allow simple communication to PC station app without additional hardware on PC side. In case of large influence of noise due to inverters, there was plan B: radio chip nRF24L01+ [13] connected to host microcontroller via SPI. In this setup PC should also have some USB–radio dongle with custom reception algorithm.
The ESP32 firmware implements serial communication with host STM32 via UART. Messages are formed in MessagePack [4] standard using open–source C implementation [1]. ESP32 converts received MessagePack message and convert it to JSON format using cJSON [5] library. All the time ESP32 is access point in which publish on broadcast address those JSON’s using UDP protocol. After receiving any JSON from station app (also through UDP) convert it back to MessagePack and send to the host.
Watchdog mechanism are added to improve safety of the communication system. If host microcontroller is not transmitting any valid MessagePack’s for more than 1 second, it broadcast JSON with error code. If station app is not transmitting and valid JSON’s for more than 1 second it send message including stop command to the host.
Due to the satisfactory level of performance of ESP32 radio module was not even developed at all. In the future, radio module will be probably removed from controller board design.

### 2.6 Station app

The network interface for communicating with the robot and the form of messages have been designed to be easy to implement in any programming language. Simple Python script can be used to receive and


(a) Receive robot state | (b) Send desired robot configuration

Figure 4: Example Python communication scripts

visualize state of the robot (ASCII characters in form of JSON through UDP) and for sending control values (picture 4). However, for USB joystick it was simpler to use C++ GUI app written using Qt [6].

## 3 Summary

Goals | Realization
Must do | custom circuit for BLDC control and sensors BEMF control algorithm on both motors controlling of servos reading IMU sensor 2-way communication using ESP32 robot movement in open-loop | fully fully fully fully fully fully
Hope to do | reading optical flow sensor 2-way communication using nRF24L01+ EKF for state estimation robot movement in close-loop (using on-board sensors) | fully not needed none none


Figure 5: Controller mounted on the robot frame

## 4 Conclusions

Main goals of the project have been achieved. Robot is able to startup motors and start moving around on the flat ground. On–board sensors are working continuously on maximum possible frequency. Current robot state can be received using wireless network as well as reference configuration for the robot. Developed hardware allow to determine pros and cons of the originally proposed solutions and serve as a good starting point for the final controller board.

## References

[1] camgunz. An implementation of the MessagePack serialization format in C. https://github.com/camgunz/cmp. (https://github.com/camgunz/cmp)
[2] J. P. Charras. KiCad. https://www.kicad.org/.
[3] Espressif. ESP32-C3 Series. https://www.espressif.com/sites/default/files/documentation/esp32-c3_datasheet_en.pdf. (https://www.espressif.com/sites/default/files/documentation/esp32-c3_datasheet_en.pdf)
[4] S. Furuhashi. Message Pack It’s like JSON. but fast and small. https://msgpack.org/index.html.
[5] Gamble, D. Ultralightweight JSON parser in ANSI C. https://github.com/DaveGamble/cJSON.
[6] Qt Group. Qt. https://www.qt.io/.
[7] PixArt Imaging Inc. PMW3901 datasheet. https://download.kamami.pl/p587092-pmw3901mb-txqt_-_productbrief_2451186_7.pdf. (https://download.kamami.pl/p587092-pmw3901mb-txqt_-_productbrief_2451186_7.pdf)
[8] InvenSense. | MPU6050 datasheet. | https://invensense.tdk.com/wp-content/uploads/2015/02/
MPU-6000-Datasheet1.pdf. (https://invensense.tdk.com/wp-content/uploads/2015/02/MPU-6000-Datasheet1.pdf)
[9] P. Joniak. Control problem for two HOG wheel mobile robot. Master’s thesis, https://kcir.pwr.edu.pl/~mucha/Pracki/Pawel_Joniak_praca_magisterska.pdf, (https://kcir.pwr.edu.pl/~mucha/Pracki/Pawel_Joniak_praca_magisterska.pdf) Wrocław University of Science and Technology, 2017.
[10] T. Lubelski. Construction of small mobile laboratory robot of class (1,2). Bachelor’s thesis, https: //kcir.pwr.edu.pl/~mucha/Pracki/Tomek_Lubelski_praca_inzynierska.pdf, Wrocław University of Science and Technology, 2023.
[11] ST Microelectronics. | STM32U535xx datasheet. | https://www.st.com/resource/en/datasheet/
stm32u535cb.pdf. (https://www.st.com/resource/en/datasheet/stm32u535cb.pdf)
[12] PTC. Onshape. https://www.onshape.com/en/.
[13] Nordic Semiconductors. nRF24L01+ Single Chip 2.4GHz Transceiver Product Specification v1.0. https: //cdn.sparkfun.com/assets/3/d/8/5/1/nRF24L01P_Product_Specification_1_0.pdf.

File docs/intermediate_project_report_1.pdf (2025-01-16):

## Project proposal Controller for Hogger² HOG wheel robot

Eryk Możdżeń

October 29, 2024

Hogger²
is a mobile robot with two HOG (Hemispherical Omnidirectional Gimbaled) (https://en.wikipedia.org/wiki/Hemispherical_omnidirectional_gimbaled_wheel) wheels belonging to KCiR. In the past, many diploma theses have been written on modeling and controlling a robot with such a drive [4], but none of them have tested them on a real robot, among other things due to the lack of efficient hardware. The goal of this project is to develop controller module (hardware and firmware) for existing chassis (described in [3]) that allows:
- controlling speed of two BLDC motors via BEMF without external controllers (built-in 2-channel triple-half bridge),
- controlling 4 servos via PWM signal,
- reading on-board sensors (6DoF IMU and maybe optical flow),
- transferring data in both ways via ESP32 (interface described in [5]) and/or NRF24L01+ radio module.

The outcome of the project will be a robot with implemented simple algorithm for movement without slippage on the flat ground. Robot should be controlled wirelessly from PC. The most challenging part will be implementation of velocity control of the two BLDC motors (hardware and software part) that will not burn the motors nor itself. Algorithm was described in [2, 1, 6].

Goals
Must do | Hope to do
- custom circuit for BLDC control and sensors • BEMF control algorithm on both motors • controlling of servos • reading IMU sensor • 2-way communication using ESP32 • robot movement in open-loop | • reading optical flow sensor • 2-way communication using NRF24L01+ • EKF for state estimation • robot movement in close-loop (using on-board sensors)

Needed tools:

- KiCad for schematic and PCB design
- STM32Cube for low-level code generation
- Qt for PC executables useful during debugging

## References

[1] Electronoobs. My open source Arduino ESC – BEMF zero-cross. YouTube tutorial. https://www.youtube.com/watch?v=VdkloigaxZo. (https://www.youtube.com/watch?v=VdkloigaxZo)
[2] GreatScott! Make your own ESC – BLDC Motor Driver. YouTube tutorial. https://www.youtube.com/watch?v=W9IHEqlGG1s. (https://www.youtube.com/watch?v=W9IHEqlGG1s)
[3] Damian Góral. Two HOG wheel mobile robot construction. Bachelor’s thesis, https://kcir.pwr.edu.pl/~mucha/Pracki/Damian_Goral_praca_inzynierska.pdf, (https://kcir.pwr.edu.pl/~mucha/Pracki/Damian_Goral_praca_inzynierska.pdf) Wrocław University of Science and Technology, 2017.
[4] Paweł Joniak. Control problem for two HOG wheel mobile robot. Master’s thesis, https://kcir.pwr.edu.pl/~mucha/Pracki/Pawel_Joniak_praca_magisterska.pdf, (https://kcir.pwr.edu.pl/~mucha/Pracki/Pawel_Joniak_praca_magisterska.pdf) Wrocław University of Science and Technology, 2017.
[5] Tomasz Lubelski. Construction of small mobile laboratory robot of class (1,2). Bachelor’s thesis, https://kcir.pwr.edu.pl/~mucha/Pracki/Tomek_Lubelski_praca_inzynierska.pdf, (https://kcir.pwr.edu.pl/~mucha/Pracki/Tomek_Lubelski_praca_inzynierska.pdf) Wrocław University of Science and Technology, 2023.
[6] STM32WROBOTYCE. Sterowanie 3-fazowym silnikiem BLDC – pomiar BEMF. Blogpost tutorial. https://www.stm32wrobotyce.pl/2021/06/30/sterowanie-3-fazowym-silnikiem-bldc-pomiar-bemf/.

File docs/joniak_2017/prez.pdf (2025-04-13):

W moje pracy poruszyłem zagadnienie sterowania robota mobilnego napędzanego dwiema wirującymi półsferami. Jest to kontynuacja badań rozpoczętych w trakcie projektu inżynierskiego. Poprzednio pokazaliśmy zalety takiego napędu w postaci dużych natychmiastowych przyśpieszeń oraz duża zwrotność takiego robota. W pracy inżynierskiej wyprowadzone zostały dwa modele robota a także pokazaliśmy podobieństwo pomiędzy wirującą półsferą a skrętnym kołem z zmiennym promieniem a przez to podobieństwo dual hoggera(tak nazwaliśmy naszego robota) a robotem z dwoma skrętnymi kołami. Celem pracy dyplomowej był zaproponowanie algorytmów sterowania. Jako dwa podstawowe zastosowane algorytmy wybraliśmy znane algorytmy ogólnego zastosowania w robotach mobilnych tzn linearyzacje statyczną i dynamiczną. Algorytmy dla wprawienia się w temat najpierw przetestowaliśmy na modelu symultanicznym w którym obie sfery wychylają się synchronicznie. Już na tym etapie napotkaliśmy na znaczącą przeszkodę mimo iż algorytmy spełniały swoją podstawową rolę to w przebiegach pojawiały się niepożądane duże oscylacje. Było dla nas oczywiste że oscylacje o tak dużej częstotliwości nie będą możliwe do zrealizowania na rzeczywistym robocie. W modelu symultanicznym zastosowanie linearyzacji dynamicznej znacząco zmniejszyło oscylacje jednak dla modelu pełnego zarówno linearyzacja statyczna jak i dynamiczna powodowała oscylacje. Kolejno podjęliśmy próbę sterowania modelem pełny poprzez przeniesienie sterowań z modelu uproszczonego tzn z dwoma skrętnymi kołami. Tutaj również wykorzystaliśmy algorytm linearyzacji statycznej i dynamicznej. Pokazaliśmy dwie metody przenoszenia sterowań: online i offline. W przenoszeniu offline najpierw wyliczaliśmy trajektorie ruchu modelu uproszczonego a następnie przeliczaliśmy je na trajektorie modelu pełnego i pochodne tak wyliczonych sygnałów podawaliśmy jako sterowania. Otrzymywane wyniki czasami były bardzo dobre (błąd rzędy kilku centymetrów a czasami modele ,,rozjeżdżały’’ się a ponieważ w przenoszeniu offline nie ma korekcji robot nie wracał a zadana trajektorię. Przeniesienie sygnało polegało na wyliczeniu sterowań w modelu uproszczonego na podstawie aktualnego stanu modelu pełnego a następnie przekształcenie tych sterowań na sterowania modelu pełnego. Odbywało się to niejako w czasie rzeczywistym i pozwalał na korekcje. Oczywiście ponieważ modele nie są dokładnie takie same błąd nigdy nie spadał do zera. Na koniec zaproponowaliśmy nowy algorytm dla modelu pełnego polegający an uproszczeniu pewnych wyrazów w macierzy G. Można wykazać że wpływ niektórych współczynników na prędkość postępową jest mała w porównaniu do innych i można całkowicie je wyeliminować. Tak uproszczona macierz może potem zostać użyta w algorytmie linearyzacji dynamicznej co daje bardzo dobre wyniki. Znikają oscylacje a błąd nie jest większy niż 0.1cm. Algorytm nazwaliśmy JPTD (Jakie Proste! To Działa!)

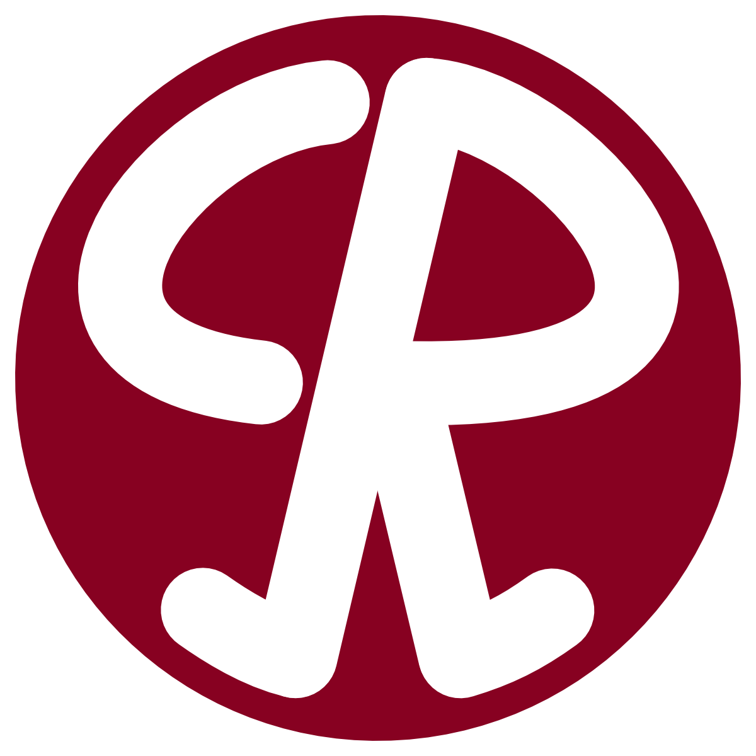
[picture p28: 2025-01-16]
hardware/resources/kcir.png

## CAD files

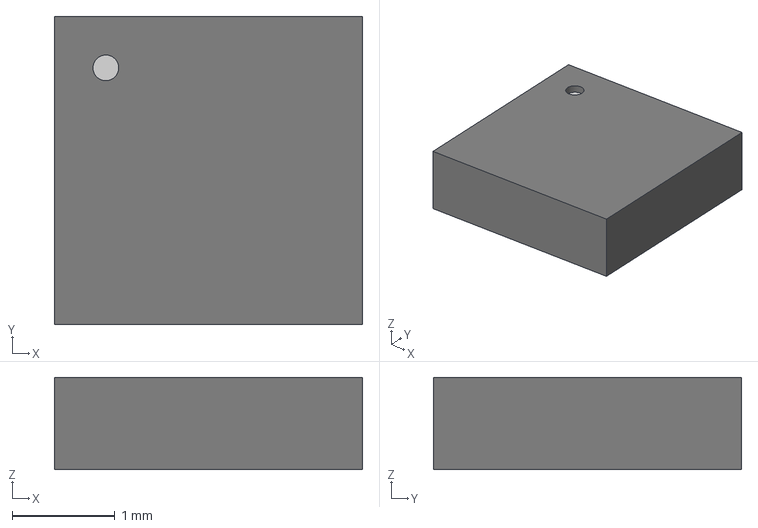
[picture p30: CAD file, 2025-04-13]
hardware/models/hmc5883l.step
3.00 x 3.00 x 0.9 mm

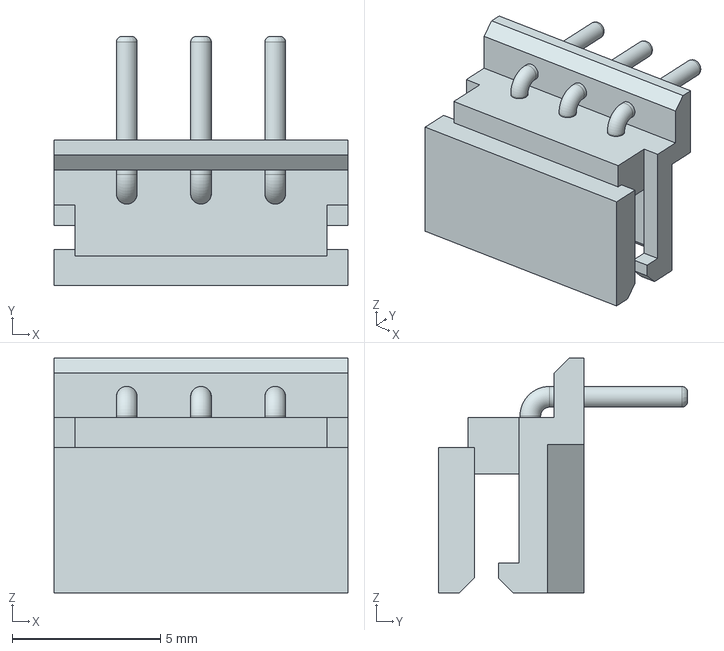
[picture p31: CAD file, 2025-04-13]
hardware/models/molex-minispox-22057035-5268.step
9.90 x 8.40 x 7.90 mm

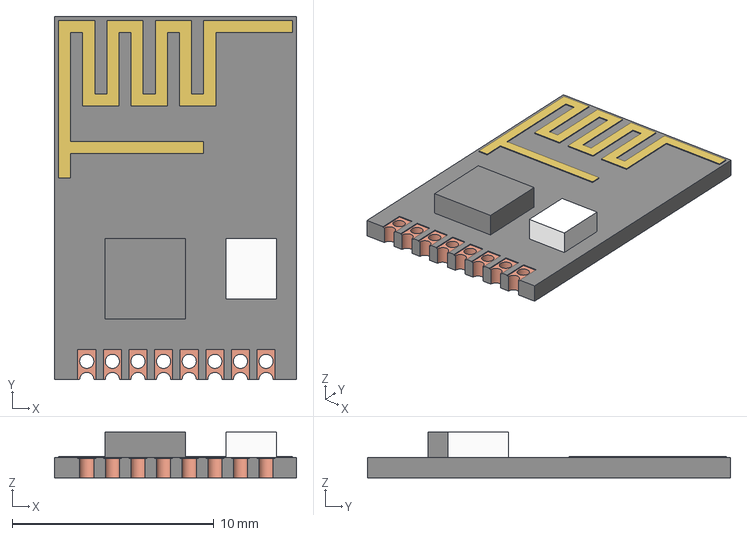
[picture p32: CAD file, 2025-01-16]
hardware/models/nrf24l01p_mini_smd.step
12.0 x 18.0 x 2.27 mm

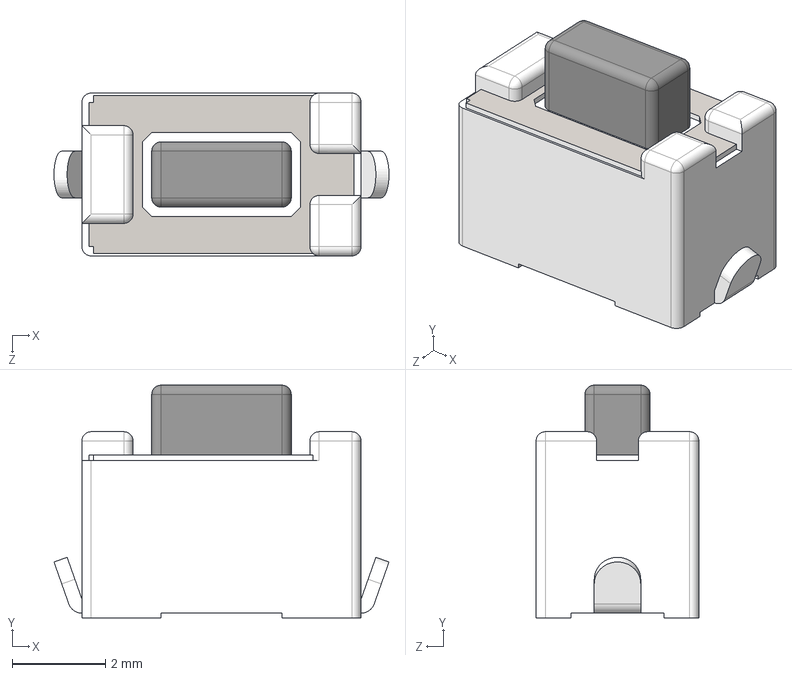
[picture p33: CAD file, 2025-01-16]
hardware/models/spst_6x3mm.step
7.20 x 5.00 x 3.50 mm

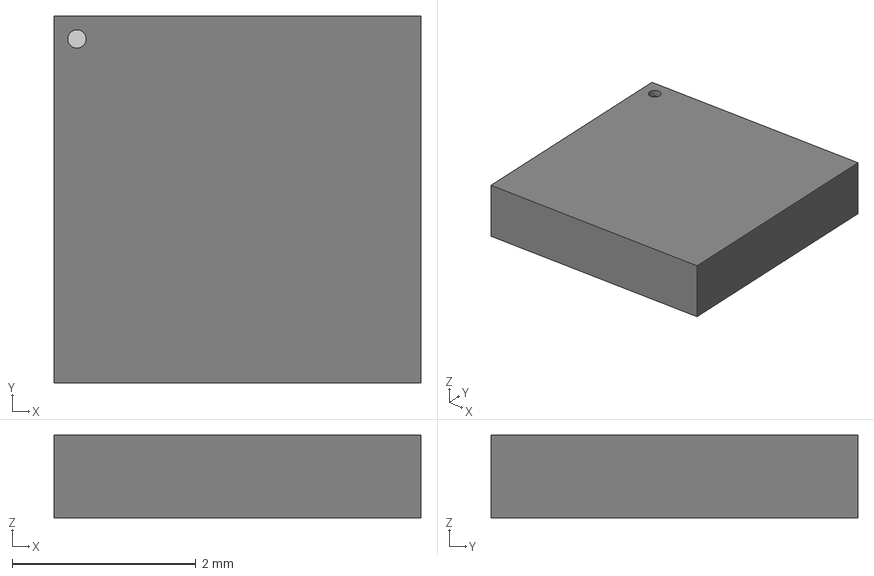
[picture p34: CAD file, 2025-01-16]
hardware/models/mpu6050.step
4.00 x 4.00 x 0.9 mm

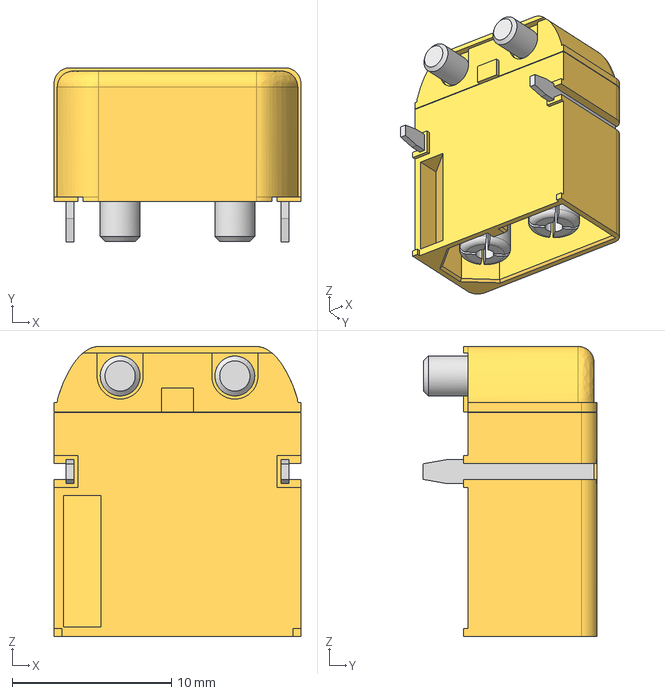
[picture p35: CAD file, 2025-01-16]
hardware/models/xt60pw-m.step
15.5 x 11.0 x 18.2 mm

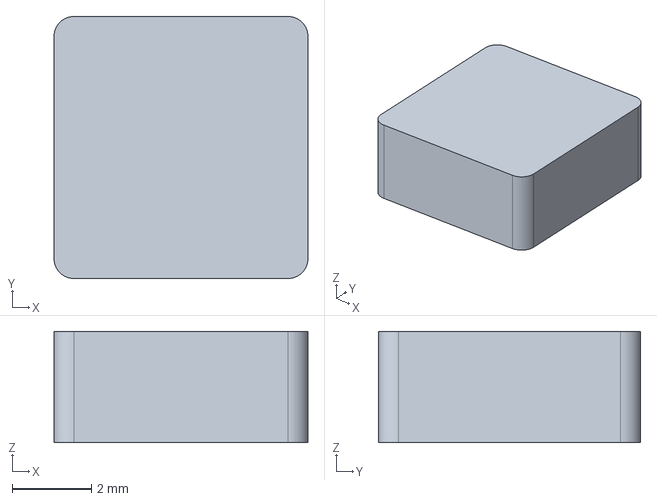
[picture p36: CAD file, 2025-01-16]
hardware/models/pa4341.xxxnlt.step
6.40 x 6.60 x 2.80 mm

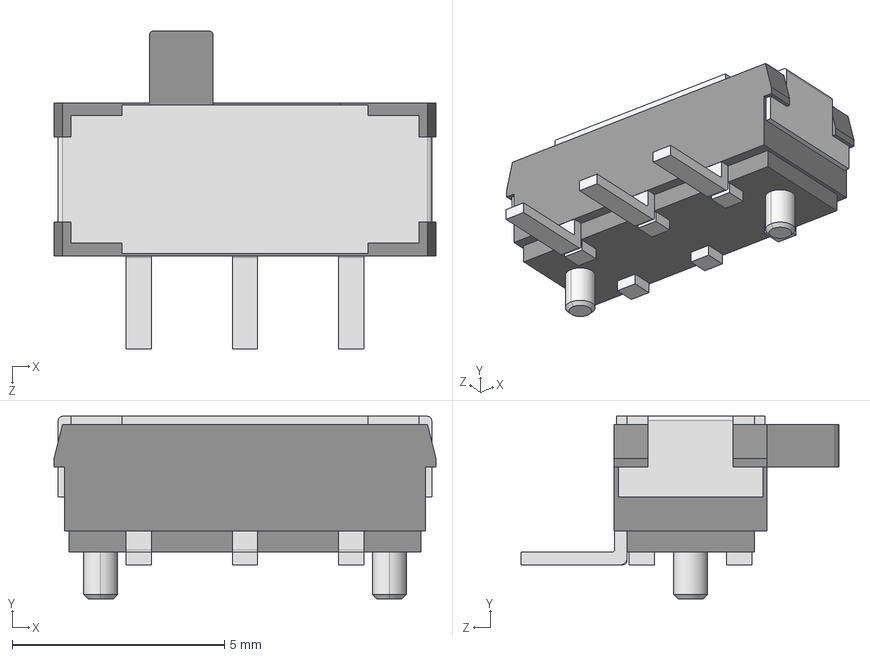
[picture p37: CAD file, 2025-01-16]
hardware/models/js102011saqn.step
9.00 x 4.30 x 7.50 mm

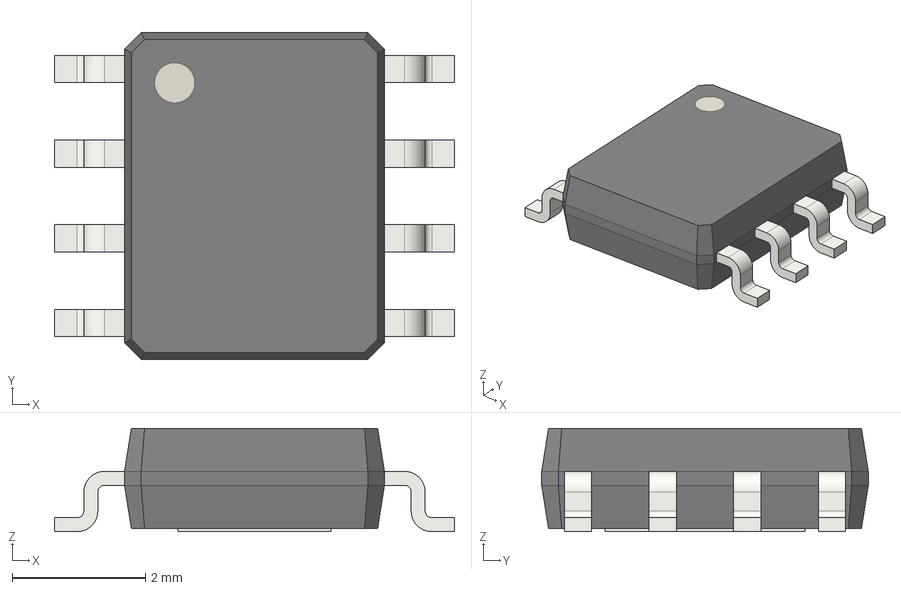
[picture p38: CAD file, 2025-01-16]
hardware/models/lv14340.step
6.00 x 4.90 x 1.55 mm

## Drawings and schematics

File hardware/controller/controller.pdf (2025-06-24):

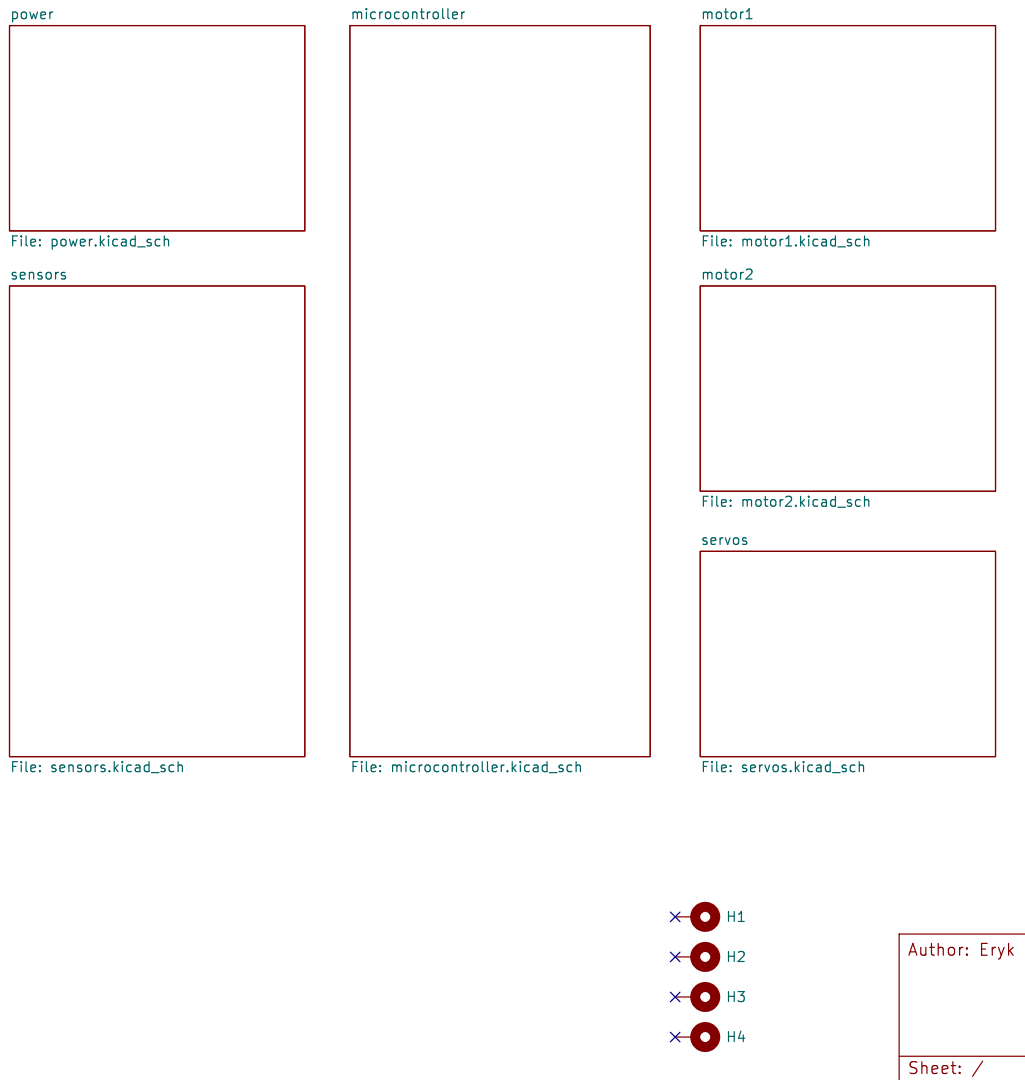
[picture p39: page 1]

servos File: servos.kicad_sch motor1 File: motor1.kicad_sch

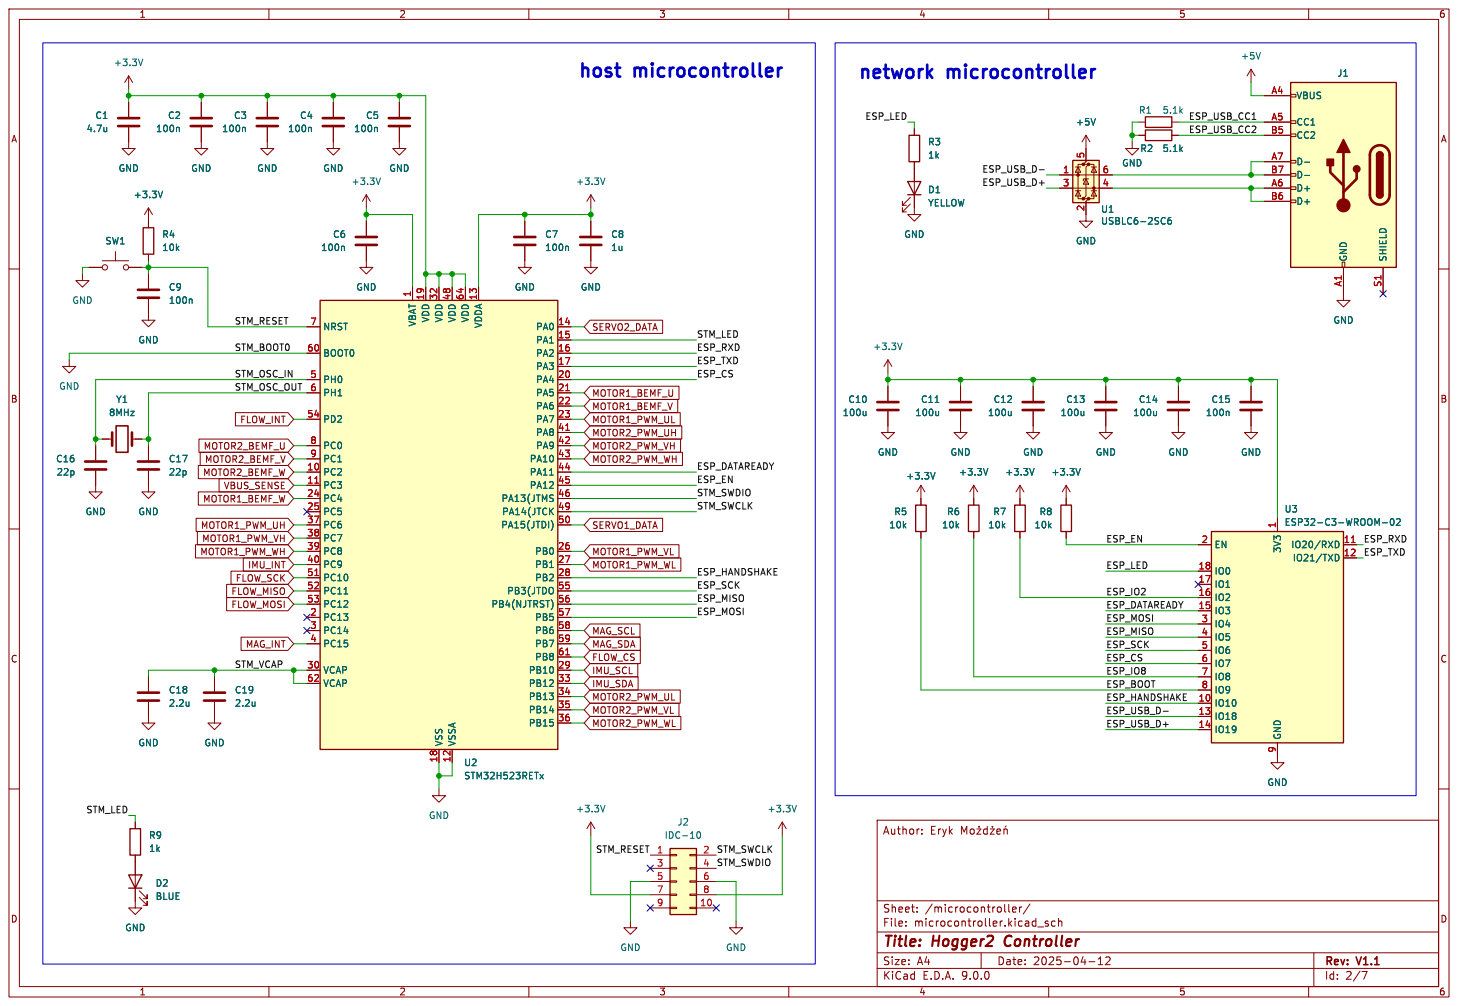
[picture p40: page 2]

1 VDD 19 VDD 32 VSS 18 VDD 48 VSSA 12 VDD 64 VDDA 13 PA0 14 PA1 15 PA2 16 PA3 17 PA4 20 PA5 21 PA6 22 PA7 23 PA8 41 PA9 42 PA10 43 PA11 44 PA12 45 PA13(JTMS 46 PA14(JTCK 49 PA15(JTDI) 50 PB0 26 PB1 27 PB2 28 PB3(JTDO 55 PB4(NJTRST) 56 PB5 57 PB6 58 PB7 59 PB8 61 PB10 29 PB12 33 PB13 34 PB14 35 PB15 36 U2STM32H523RETx GND GND GND

1 VDD 19 VDD 32 VSS 18 VDD 48 VSSA 12 VDD 64 VDDA 13 PA0 14 PA1 15 PA2 16 PA3 17 PA4 20 PA5 21 PA6 22 PA7 23 PA8 41 PA9 42 PA10 43 PA11 44 PA12 45 PA13(JTMS 46 PA14(JTCK 49 PA15(JTDI) 50 PB0 26 PB1 27 PB2 28 PB3(JTDO 55 PB4(NJTRST) 56 PB5 57 PB6 58 PB7 59 PB8 61 PB10 29 PB12 33 PB13 34 PB14 35 PB15 36 GND

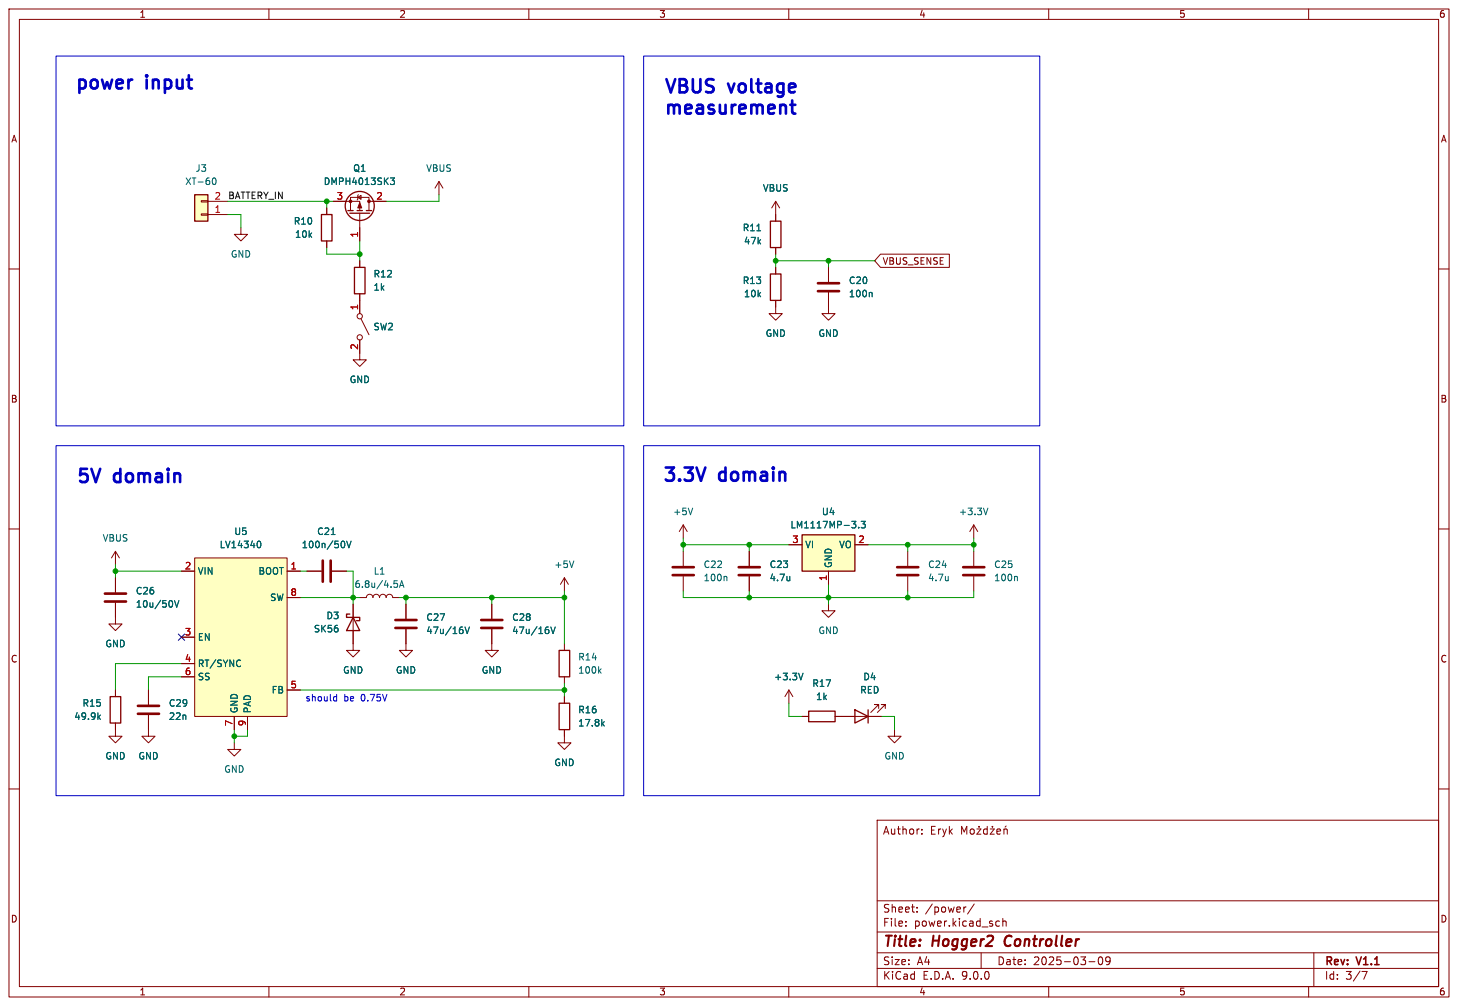
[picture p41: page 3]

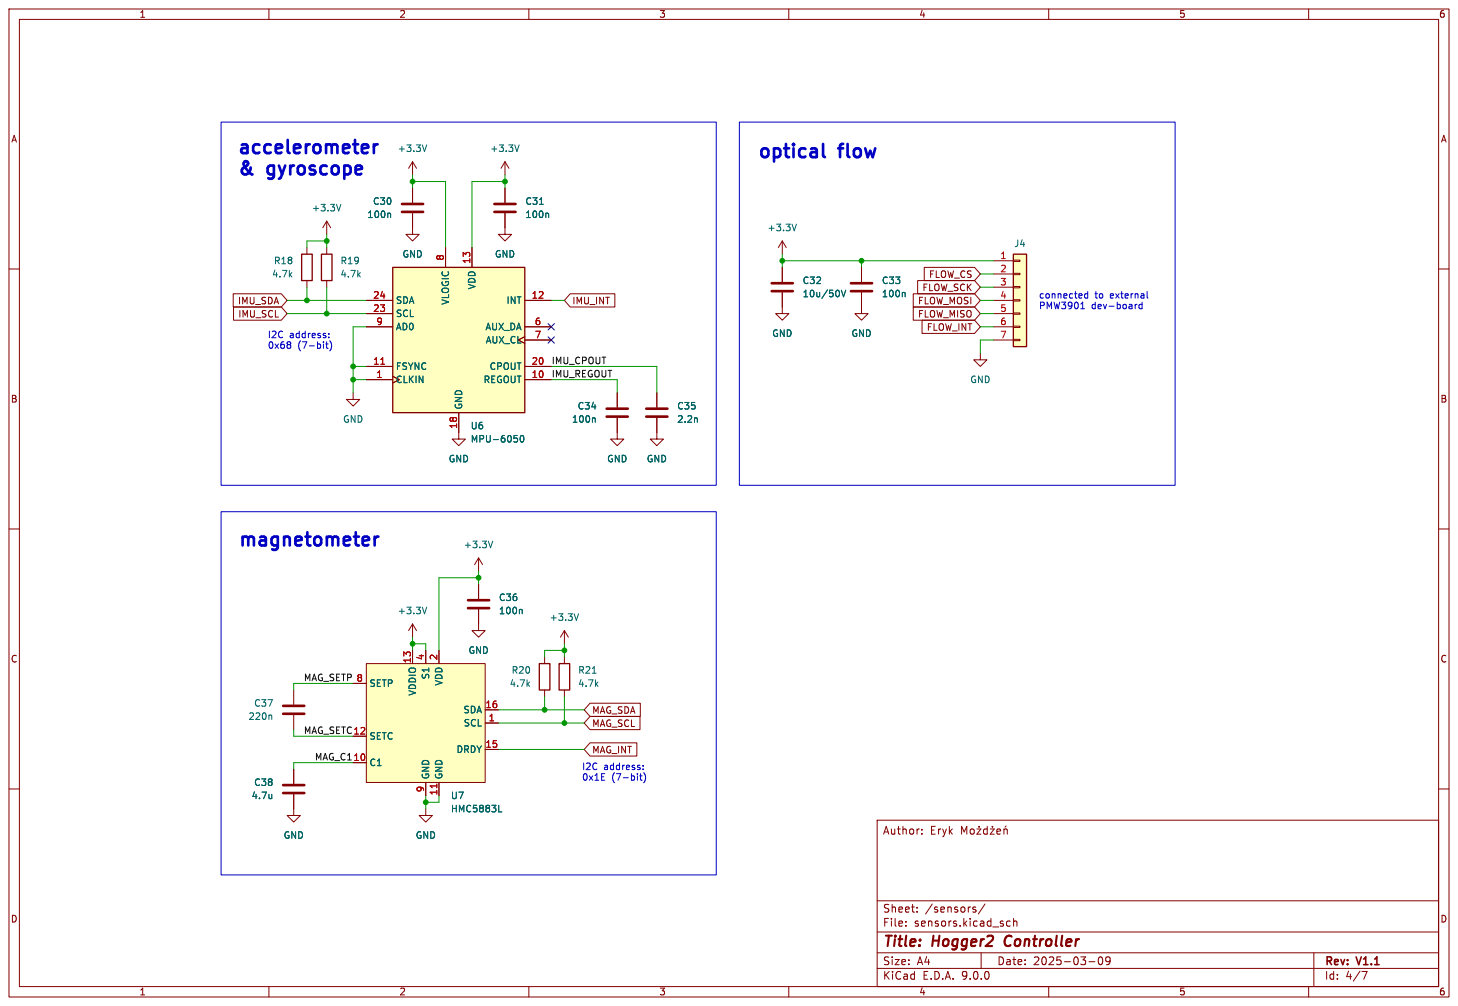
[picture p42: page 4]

2 GND 11 SDA 16 SCL 1 DRDY 15 GND GND

2 GND 11 SDA 16 SCL 1 DRDY 15 U7 HMC5883L

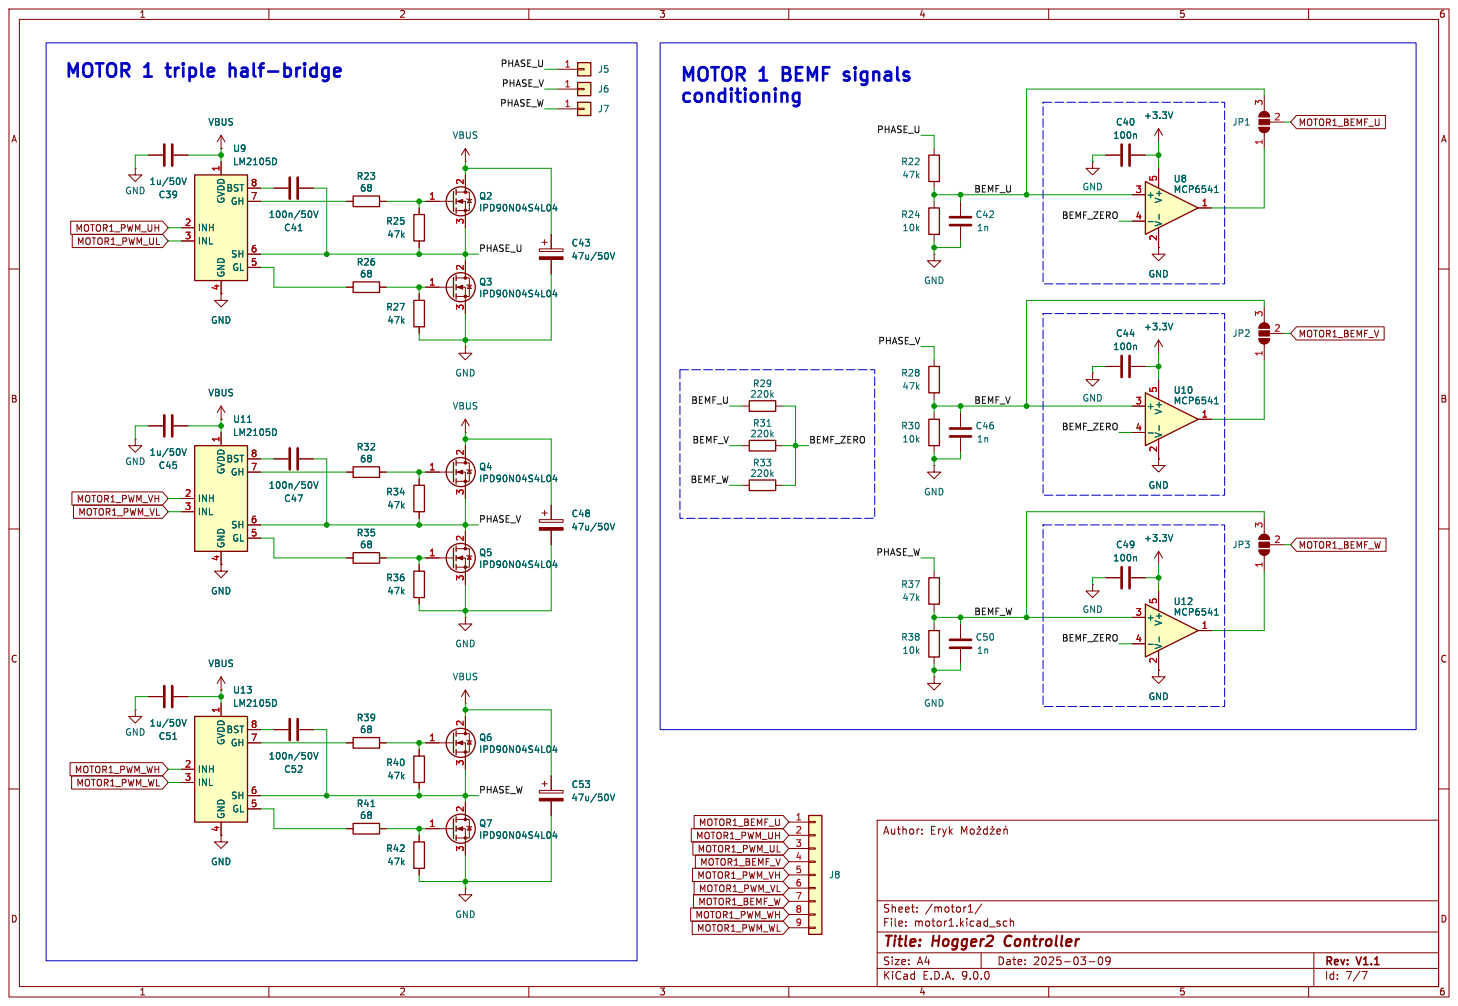
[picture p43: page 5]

MOTOR 1 triple half-bridge

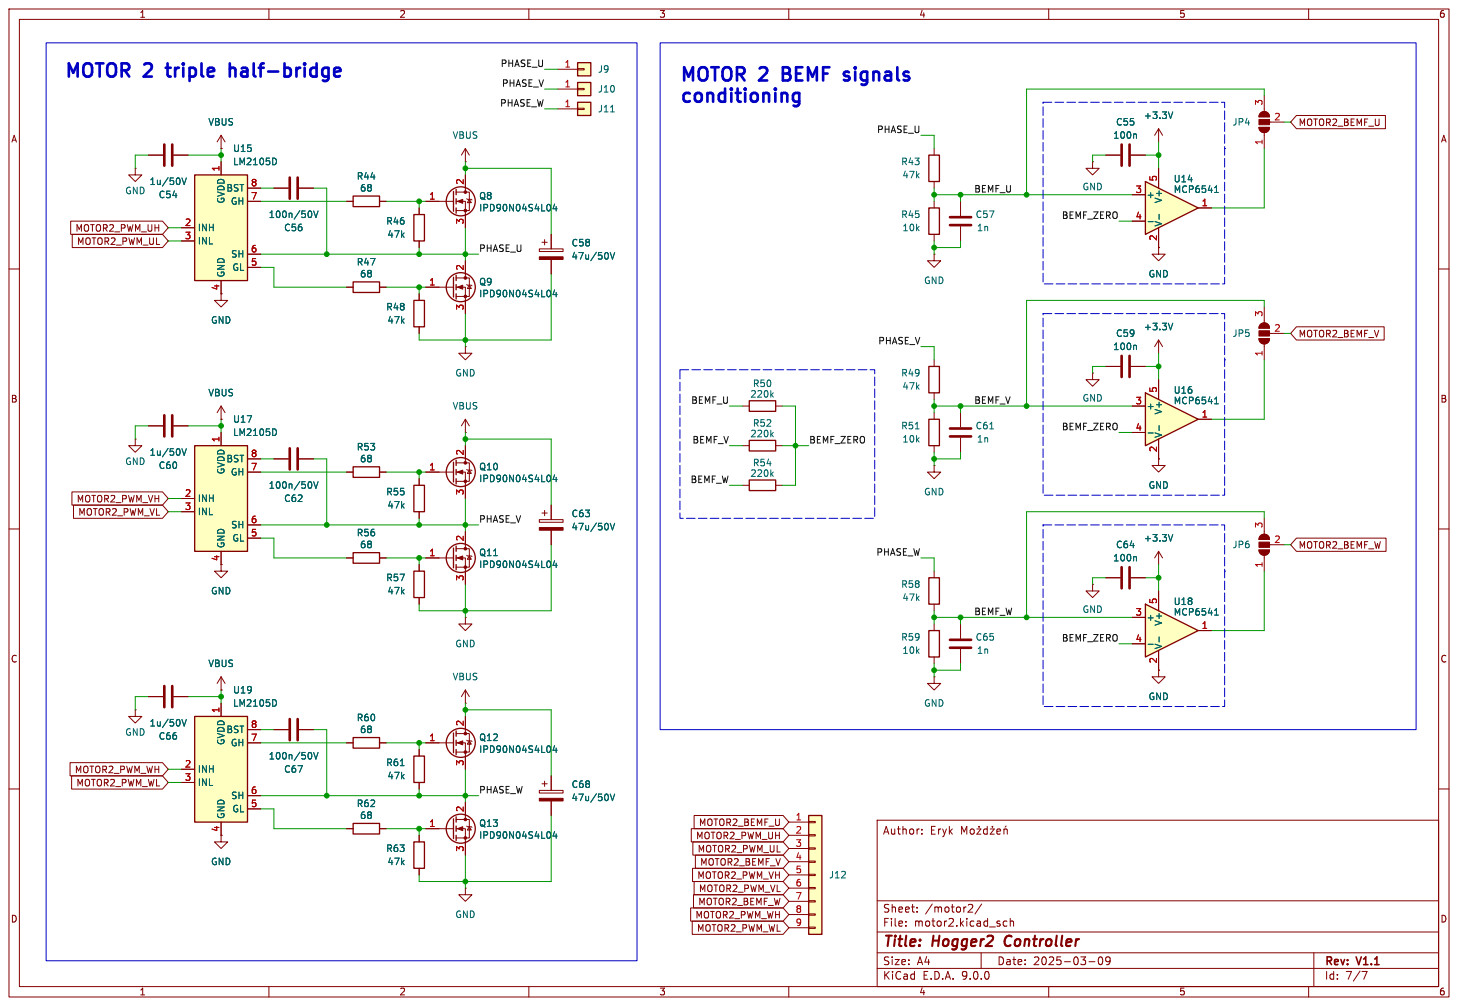
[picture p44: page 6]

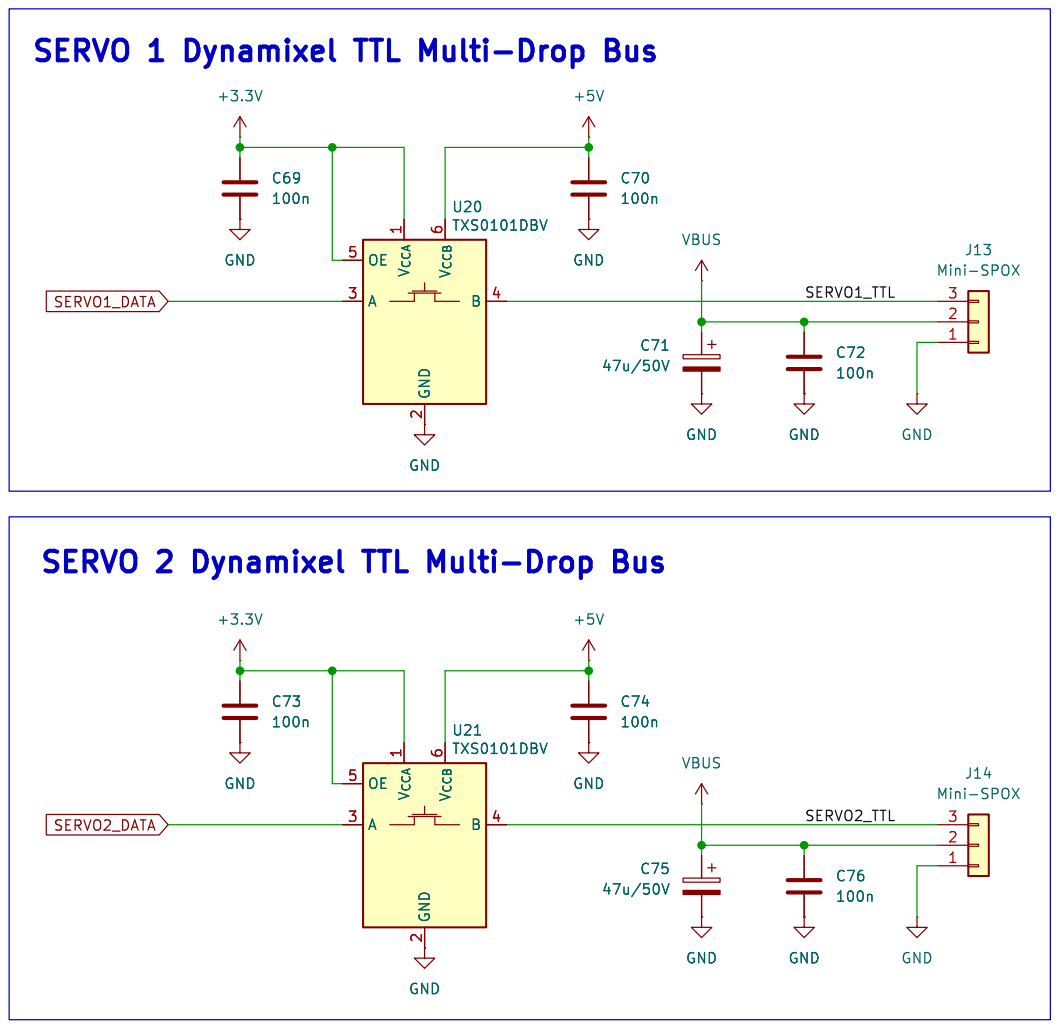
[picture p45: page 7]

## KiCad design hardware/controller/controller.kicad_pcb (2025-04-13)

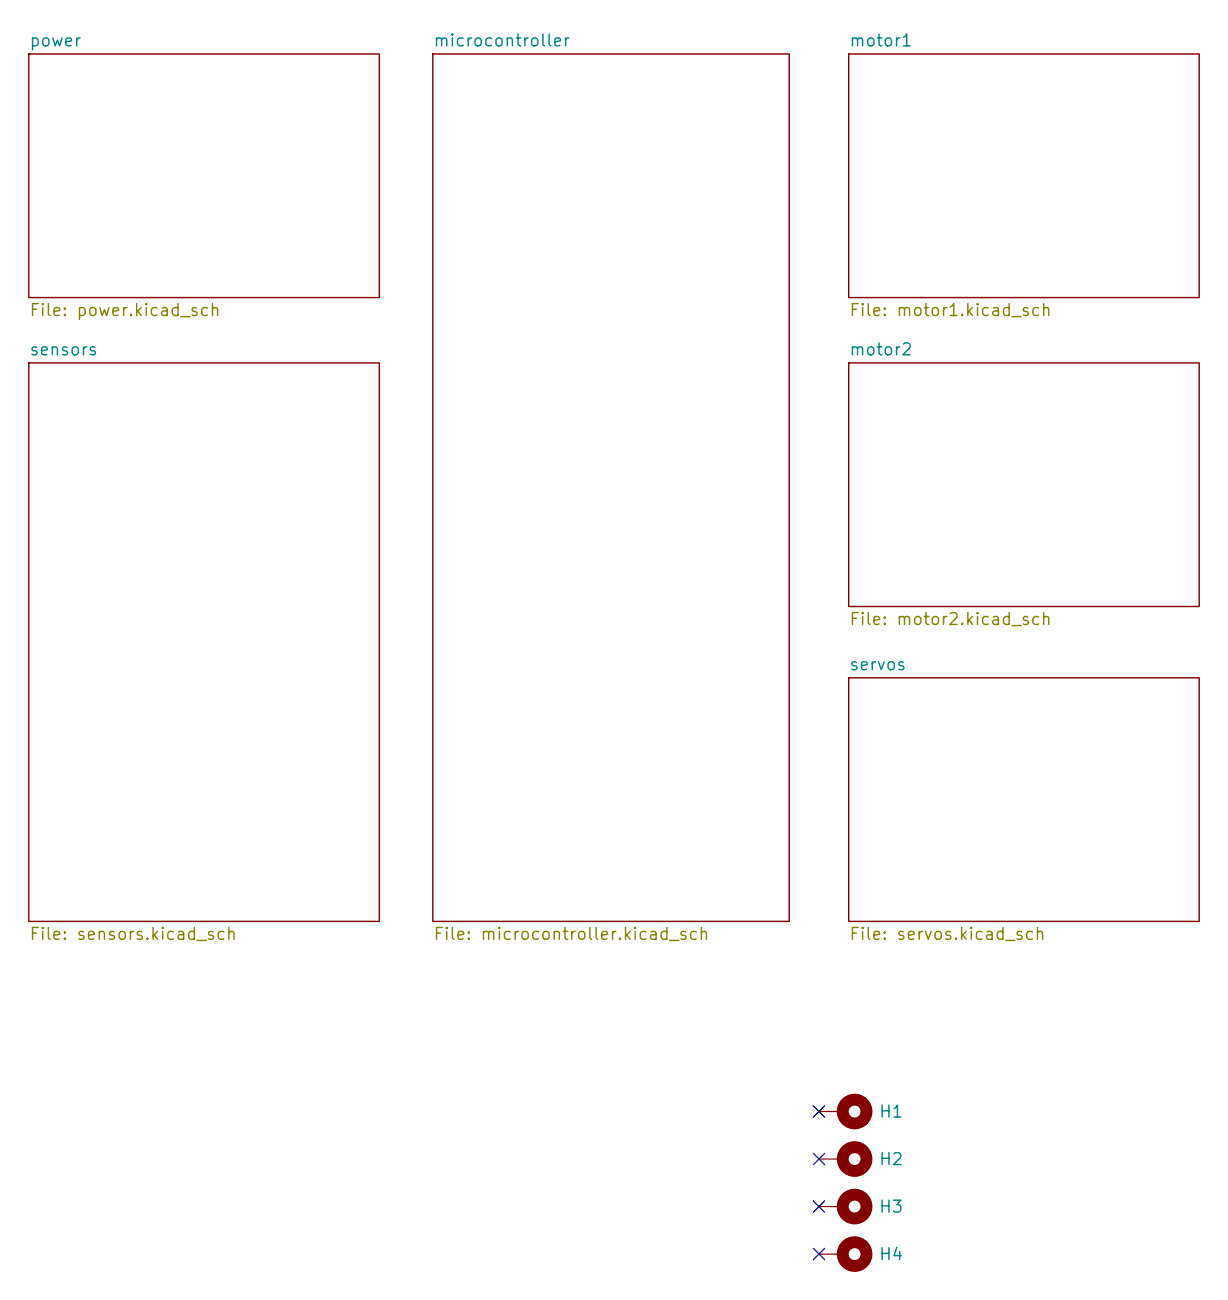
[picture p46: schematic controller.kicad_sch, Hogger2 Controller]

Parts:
H1, H2, H3, H4: MountingHole_Pad; MountingHole_3.2mm_M3_Pad_Via

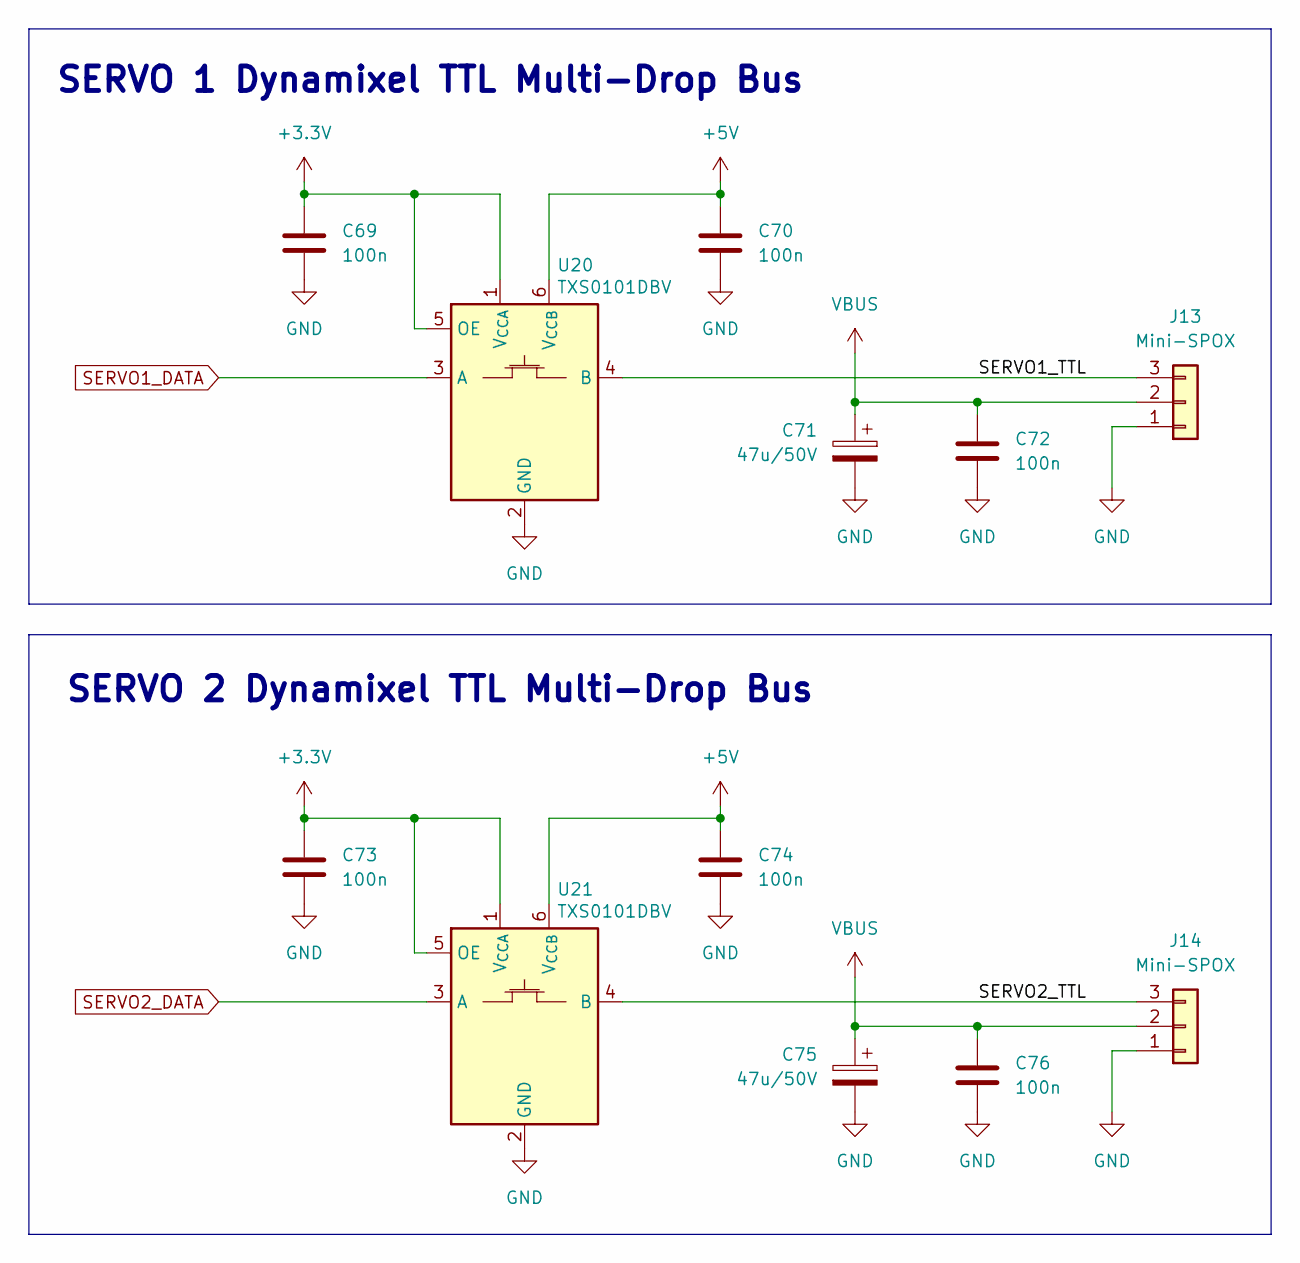
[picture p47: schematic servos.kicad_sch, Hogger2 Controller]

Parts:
C69, C70, C72, C73, C74, C76: 100n; C_0603_1608Metric
C71, C75: 47u/50V; CP_Elec_6.3x7.7
J13, J14: Mini-SPOX; Molex-MiniSPOX-22057035-5268
U20, U21: TXS0101DBV; SOT-23-6

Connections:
+3.3V: C69.1, C73.1, U20.1 (V_{CCA}), U20.5 (OE), U21.1 (V_{CCA}), U21.5 (OE); also elsewhere on the board
+5V: C70.1, C74.1, U20.6 (V_{CCB}), U21.6 (V_{CCB}); also elsewhere on the board
/servos/SERVO1_TTL: J13.3, U20.4 (B)
/servos/SERVO2_TTL: J14.3, U21.4 (B)
GND: C69.2, C70.2, C71.2, C72.2, C73.2, C74.2, C75.2, C76.2, J13.1, J14.1, U20.2 (GND), U21.2 (GND); also elsewhere on the board
SERVO1_DATA: U20.3 (A); also elsewhere on the board
SERVO2_DATA: U21.3 (A); also elsewhere on the board
VBUS: C71.1, C72.1, C75.1, C76.1, J13.2, J14.2; also elsewhere on the board

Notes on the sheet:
SERVO 1 Dynamixel TTL Multi-Drop Bus
SERVO 2 Dynamixel TTL Multi-Drop Bus

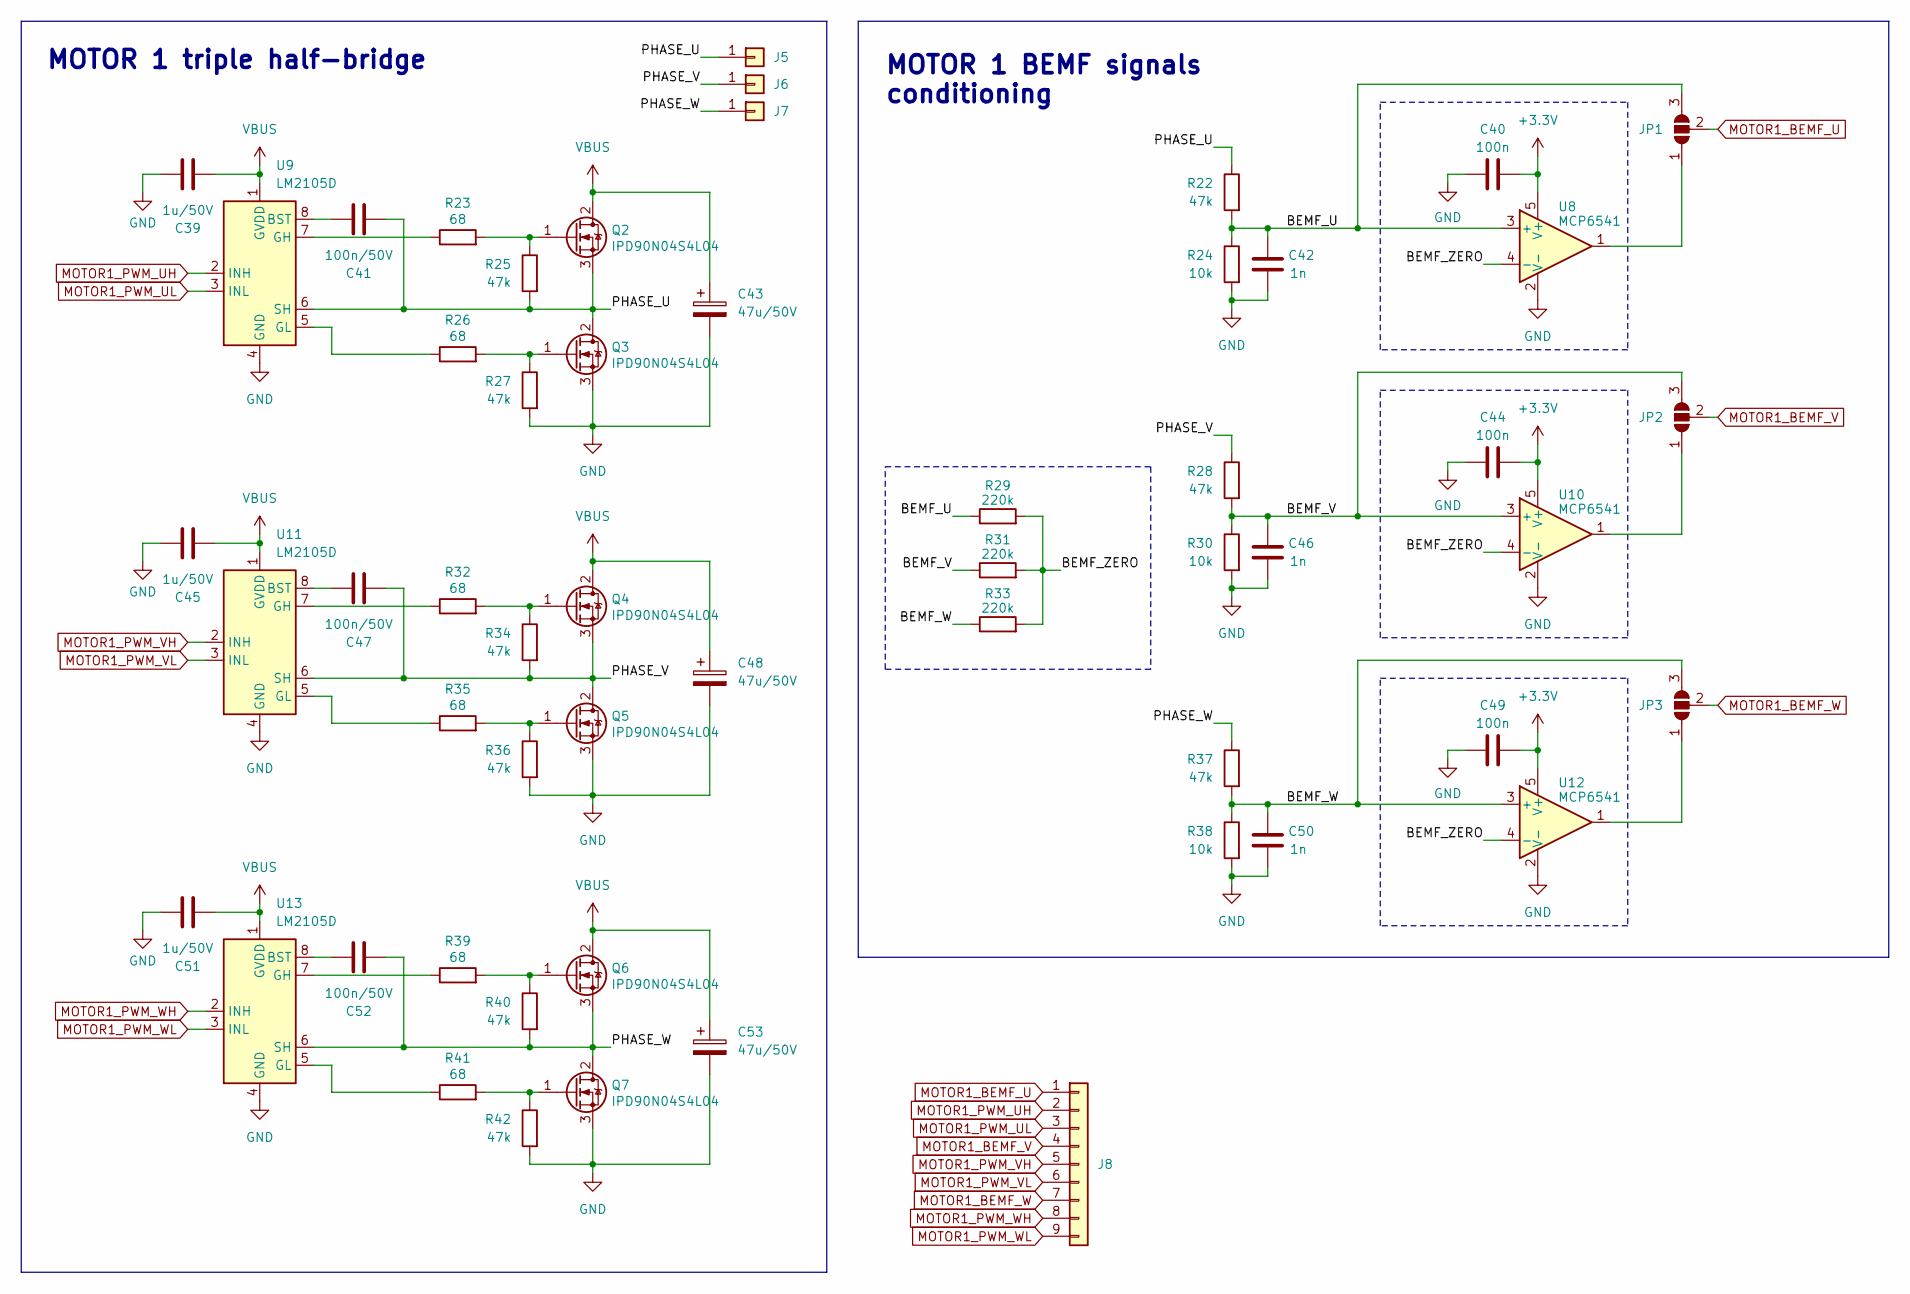
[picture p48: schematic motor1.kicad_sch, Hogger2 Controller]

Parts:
C39, C45, C51: 1u/50V; C_0603_1608Metric
C40, C44, C49: 100n; C_0603_1608Metric
C41, C47, C52: 100n/50V; C_0603_1608Metric
C42, C46, C50: 1n; C_0603_1608Metric
C43, C48, C53: 47u/50V; CP_Elec_6.3x7.7
J5, J6, J7: Conn_01x01; SolderWire-2.5sqmm_1x01_D2.4mm_OD4.4mm
J8: Conn_01x09; PinHeader_1x09_P2.54mm_Vertical
JP1, JP2, JP3: SolderJumper_3_Open; SolderJumper-3_P1.3mm_Open_RoundedPad1.0x1.5mm
Q2, Q3, Q4, Q5, Q6, Q7: IPD90N04S4L04; TO-252-2
R22, R25, R27, R28, R34, R36, R37, R40, R42: 47k; R_0603_1608Metric
R23, R26, R32, R35, R39, R41: 68; R_0603_1608Metric
R24, R30, R38: 10k; R_0603_1608Metric
R29, R31, R33: 220k; R_0603_1608Metric
U8, U10, U12: MCP6541; SOT-23-5
U9, U11, U13: LM2105D; SOIC-8_3.9x4.9mm_P1.27mm

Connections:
+3.3V: C40.2, C44.2, C49.2, U8.5 (V+), U10.5 (V+), U12.5 (V+); also elsewhere on the board
/motor1/BEMF_U: C42.1, JP1.3 (B), R22.2, R24.1, R29.1, U8.3 (+)
/motor1/BEMF_V: C46.1, JP2.3 (B), R28.2, R30.1, R31.1, U10.3 (+)
/motor1/BEMF_W: C50.1, JP3.3 (B), R33.1, R37.2, R38.1, U12.3 (+)
/motor1/BEMF_ZERO: R29.2, R31.2, R33.2, U8.4 (-), U10.4 (-), U12.4 (-)
/motor1/PHASE_U: C41.2, J5.1, Q2.3 (S), Q3.2 (D), R22.1, R25.2, U9.6 (SH)
/motor1/PHASE_V: C47.2, J6.1, Q4.3 (S), Q5.2 (D), R28.1, R34.2, U11.6 (SH)
/motor1/PHASE_W: C52.2, J7.1, Q6.3 (S), Q7.2 (D), R37.1, R40.2, U13.6 (SH)
GND: C39.1, C40.1, C42.2, C43.2, C44.1, C45.1, C46.2, C48.2, C49.1, C50.2, C51.1, C53.2, Q3.3 (S), Q5.3 (S), Q7.3 (S), R24.2, R27.2, R30.2, R36.2, R38.2, R42.2, U8.2 (V-), U9.4 (GND), U10.2 (V-), U11.4 (GND), U12.2 (V-), U13.4 (GND); also elsewhere on the board
MOTOR1_BEMF_U: J8.1, JP1.2 (C); also elsewhere on the board
MOTOR1_BEMF_V: J8.4, JP2.2 (C); also elsewhere on the board
MOTOR1_BEMF_W: J8.7, JP3.2 (C); also elsewhere on the board
MOTOR1_PWM_UH: J8.2, U9.2 (INH); also elsewhere on the board
MOTOR1_PWM_UL: J8.3, U9.3 (INL); also elsewhere on the board
MOTOR1_PWM_VH: J8.5, U11.2 (INH); also elsewhere on the board
MOTOR1_PWM_VL: J8.6, U11.3 (INL); also elsewhere on the board
MOTOR1_PWM_WH: J8.8, U13.2 (INH); also elsewhere on the board
MOTOR1_PWM_WL: J8.9, U13.3 (INL); also elsewhere on the board
unnamed: JP1.1 (A), U8.1
unnamed: JP2.1 (A), U10.1
unnamed: JP3.1 (A), U12.1
unnamed: Q2.1 (G), R23.2, R25.1
unnamed: Q3.1 (G), R26.2, R27.1
unnamed: Q4.1 (G), R32.2, R34.1
unnamed: Q5.1 (G), R35.2, R36.1
unnamed: Q6.1 (G), R39.2, R40.1
unnamed: Q7.1 (G), R41.2, R42.1
unnamed: C41.1, U9.8 (BST)
unnamed: R23.1, U9.7 (GH)
unnamed: R26.1, U9.5 (GL)
unnamed: C47.1, U11.8 (BST)
unnamed: R32.1, U11.7 (GH)
unnamed: R35.1, U11.5 (GL)
unnamed: C52.1, U13.8 (BST)
unnamed: R39.1, U13.7 (GH)
unnamed: R41.1, U13.5 (GL)
VBUS: C39.2, C43.1, C45.2, C48.1, C51.2, C53.1, Q2.2 (D), Q4.2 (D), Q6.2 (D), U9.1 (GVDD), U11.1 (GVDD), U13.1 (GVDD); also elsewhere on the board

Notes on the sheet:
MOTOR 1 triple half-bridge
MOTOR 1 BEMF signals conditioning

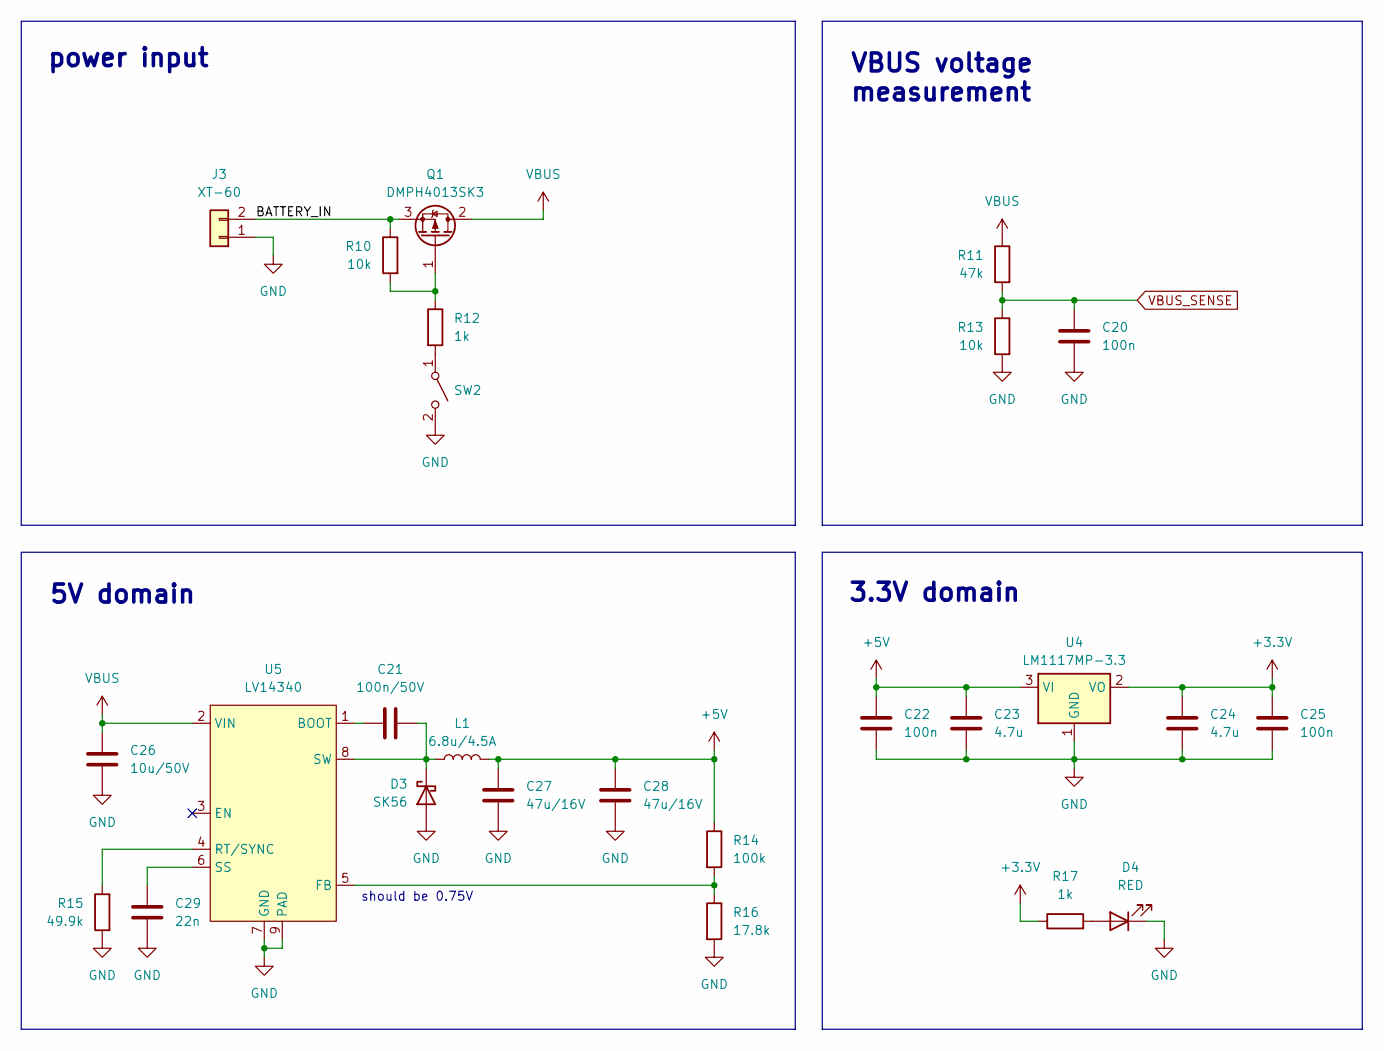
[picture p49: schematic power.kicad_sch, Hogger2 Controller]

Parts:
C20, C22, C25: 100n; C_0603_1608Metric
C21: 100n/50V; C_0603_1608Metric
C23, C24: 4.7u; C_0603_1608Metric
C26: 10u/50V; C_1206_3216Metric
C27, C28: 47u/16V; C_1210_3225Metric
C29: 22n; C_0603_1608Metric
D3: SK56; D_SMB
D4: RED; LED_0603_1608Metric
J3: XT-60; XT60PW-M
L1: 6.8u/4.5A; PA4341.XXXNLT
Q1: DMPH4013SK3; TO-252-2
R10, R13: 10k; R_0603_1608Metric
R11: 47k; R_0603_1608Metric
R12, R17: 1k; R_0603_1608Metric
R14: 100k; R_0603_1608Metric
R15: 49.9k; R_0603_1608Metric
R16: 17.8k; R_0603_1608Metric
SW2: SW_SPST; JS102011SAQN
U4: LM1117MP-3.3; SOT-223-3_TabPin2
U5: LV14340

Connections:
+3.3V: C24.1, C25.1, R17.1, U4.2 (VO); also elsewhere on the board
+5V: C22.1, C23.1, C27.1, C28.1, L1.2, R14.1, U4.3 (VI); also elsewhere on the board
/power/BATTERY_IN: J3.2, Q1.3 (S), R10.1
GND: C20.2, C22.2, C23.2, C24.2, C25.2, C26.2, C27.2, C28.2, C29.2, D3.2 (A), D4.1 (K), J3.1, R13.2, R15.2, R16.2, SW2.2 (B), U4.1 (GND), U5.7 (GND), U5.9 (PAD); also elsewhere on the board
unnamed: C21.2, D3.1 (K), L1.1, U5.8 (SW)
unnamed: D4.2 (A), R17.2
unnamed: Q1.1 (G), R10.2, R12.1
unnamed: R12.2, SW2.1 (A)
unnamed: C21.1, U5.1 (BOOT)
unnamed: R14.2, R16.1, U5.5 (FB)
unnamed: R15.1, U5.4 (RT/SYNC)
unnamed: C29.1, U5.6 (SS)
VBUS: C26.1, Q1.2 (D), R11.1, U5.2 (VIN); also elsewhere on the board
VBUS_SENSE: C20.1, R11.2, R13.1; also elsewhere on the board

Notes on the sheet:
5V domain
VBUS voltage measurement
3.3V domain
should be 0.75V
power input

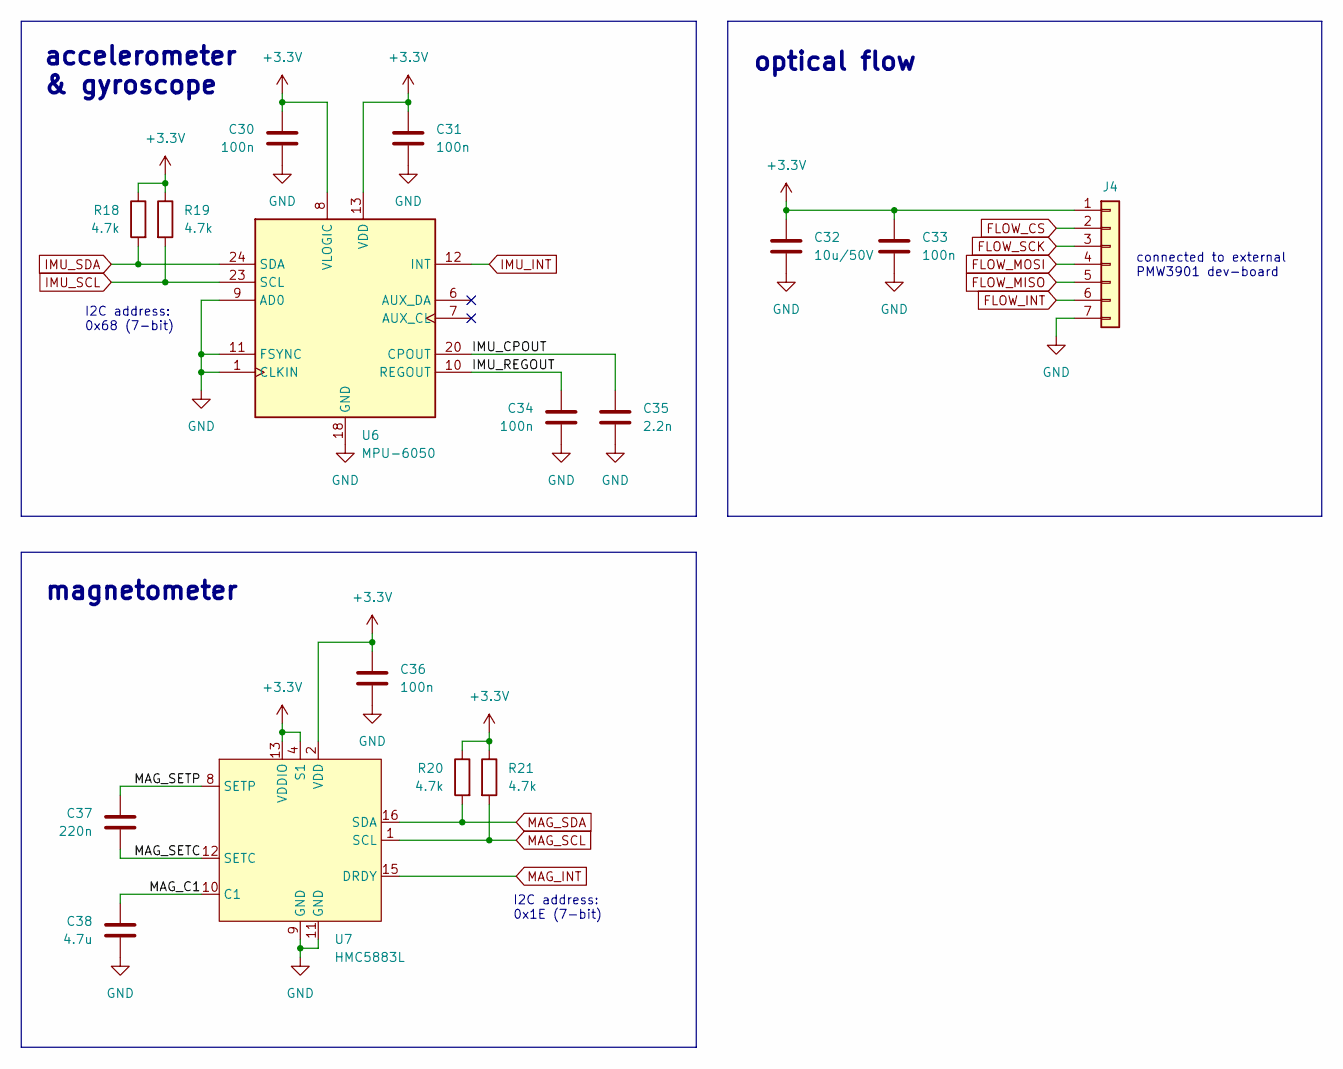
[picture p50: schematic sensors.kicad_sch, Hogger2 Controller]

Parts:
C30, C31, C33, C34, C36: 100n; C_0603_1608Metric
C32: 10u/50V; C_1206_3216Metric
C35: 2.2n; C_0603_1608Metric
C37: 220n; C_0603_1608Metric
C38: 4.7u; C_0603_1608Metric
J4: Conn_01x07; PinHeader_1x07_P2.54mm_Horizontal
R18, R19, R20, R21: 4.7k; R_0603_1608Metric
U6: MPU-6050; MPU6050_handsolder
U7: HMC5883L; HMC5883L_handsolder

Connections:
+3.3V: C30.1, C31.1, C32.1, C33.1, C36.1, J4.1, R18.1, R19.1, R20.1, R21.1, U6.8 (VLOGIC), U6.13 (VDD), U7.2 (VDD), U7.4 (S1), U7.13 (VDDIO); also elsewhere on the board
/sensors/IMU_CPOUT: C35.1, U6.20 (CPOUT)
/sensors/IMU_REGOUT: C34.1, U6.10 (REGOUT)
/sensors/MAG_C1: C38.1, U7.10 (C1)
/sensors/MAG_SETC: C37.2, U7.12 (SETC)
/sensors/MAG_SETP: C37.1, U7.8 (SETP)
FLOW_CS: J4.2; also elsewhere on the board
FLOW_INT: J4.6; also elsewhere on the board
FLOW_MISO: J4.5; also elsewhere on the board
FLOW_MOSI: J4.4; also elsewhere on the board
FLOW_SCK: J4.3; also elsewhere on the board
GND: C30.2, C31.2, C32.2, C33.2, C34.2, C35.2, C36.2, C38.2, J4.7, U6.1 (CLKIN), U6.9 (AD0), U6.11 (FSYNC), U6.18 (GND), U7.9 (GND), U7.11 (GND); also elsewhere on the board
IMU_INT: U6.12 (INT); also elsewhere on the board
IMU_SCL: R19.2, U6.23 (SCL); also elsewhere on the board
IMU_SDA: R18.2, U6.24 (SDA); also elsewhere on the board
MAG_INT: U7.15 (DRDY); also elsewhere on the board
MAG_SCL: R21.2, U7.1 (SCL); also elsewhere on the board
MAG_SDA: R20.2, U7.16 (SDA); also elsewhere on the board

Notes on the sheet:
accelerometer & gyroscope
connected to external PMW3901 dev-board
I2C address: 0x68 (7-bit)
magnetometer
optical flow
I2C address: 0x1E (7-bit)

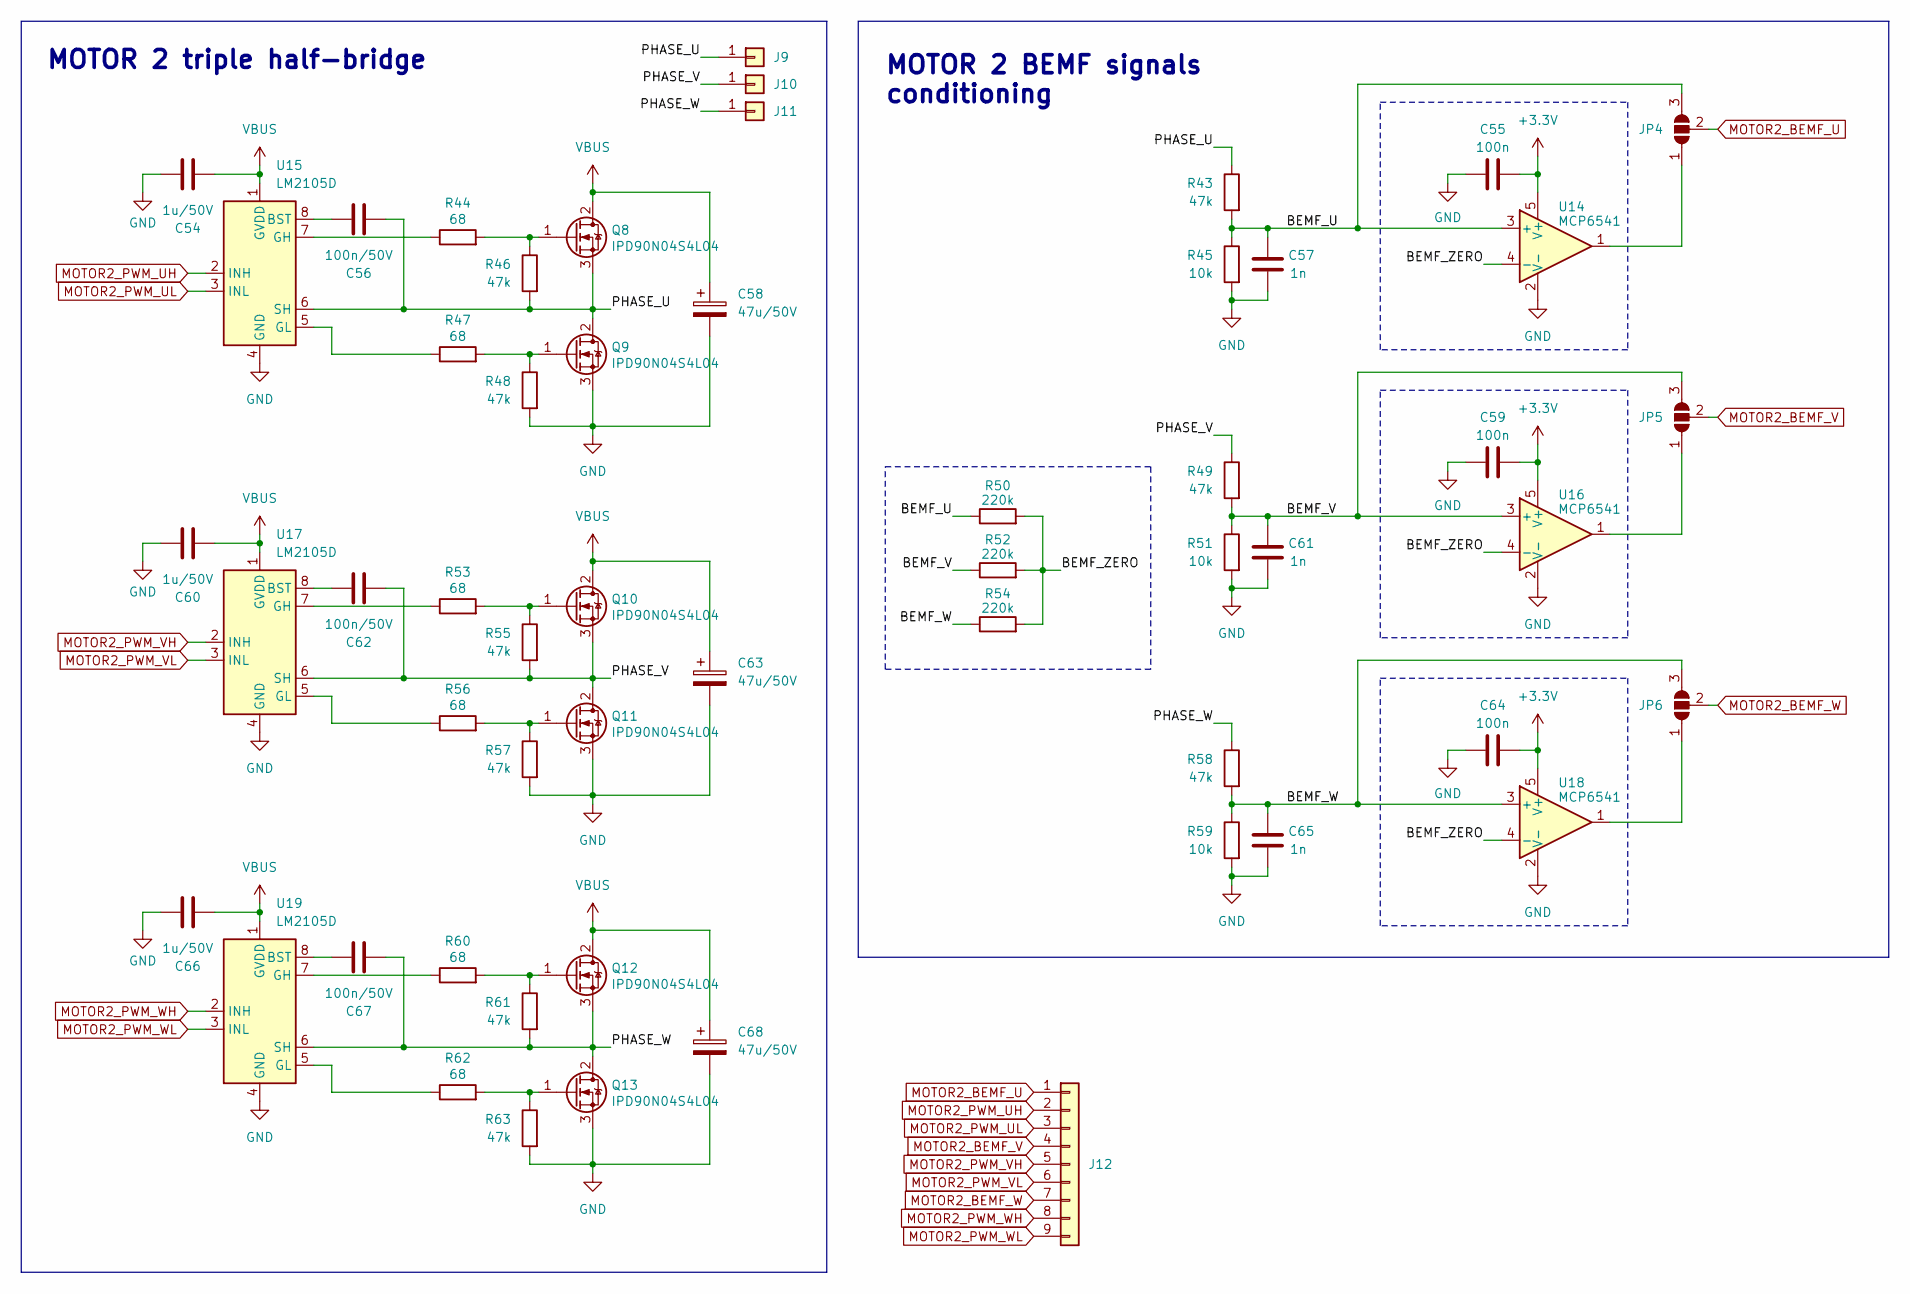
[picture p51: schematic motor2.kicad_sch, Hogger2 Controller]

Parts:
C54, C60, C66: 1u/50V; C_0603_1608Metric
C55, C59, C64: 100n; C_0603_1608Metric
C56, C62, C67: 100n/50V; C_0603_1608Metric
C57, C61, C65: 1n; C_0603_1608Metric
C58, C63, C68: 47u/50V; CP_Elec_6.3x7.7
J9, J10, J11: Conn_01x01; SolderWire-2.5sqmm_1x01_D2.4mm_OD4.4mm
J12: Conn_01x09; PinHeader_1x09_P2.54mm_Vertical
JP4, JP5, JP6: SolderJumper_3_Open; SolderJumper-3_P1.3mm_Open_RoundedPad1.0x1.5mm
Q8, Q9, Q10, Q11, Q12, Q13: IPD90N04S4L04; TO-252-2
R43, R46, R48, R49, R55, R57, R58, R61, R63: 47k; R_0603_1608Metric
R44, R47, R53, R56, R60, R62: 68; R_0603_1608Metric
R45, R51, R59: 10k; R_0603_1608Metric
R50, R52, R54: 220k; R_0603_1608Metric
U14, U16, U18: MCP6541; SOT-23-5
U15, U17, U19: LM2105D; SOIC-8_3.9x4.9mm_P1.27mm

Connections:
+3.3V: C55.2, C59.2, C64.2, U14.5 (V+), U16.5 (V+), U18.5 (V+); also elsewhere on the board
/motor2/BEMF_U: C57.1, JP4.3 (B), R43.2, R45.1, R50.1, U14.3 (+)
/motor2/BEMF_V: C61.1, JP5.3 (B), R49.2, R51.1, R52.1, U16.3 (+)
/motor2/BEMF_W: C65.1, JP6.3 (B), R54.1, R58.2, R59.1, U18.3 (+)
/motor2/BEMF_ZERO: R50.2, R52.2, R54.2, U14.4 (-), U16.4 (-), U18.4 (-)
/motor2/PHASE_U: C56.2, J9.1, Q8.3 (S), Q9.2 (D), R43.1, R46.2, U15.6 (SH)
/motor2/PHASE_V: C62.2, J10.1, Q10.3 (S), Q11.2 (D), R49.1, R55.2, U17.6 (SH)
/motor2/PHASE_W: C67.2, J11.1, Q12.3 (S), Q13.2 (D), R58.1, R61.2, U19.6 (SH)
GND: C54.1, C55.1, C57.2, C58.2, C59.1, C60.1, C61.2, C63.2, C64.1, C65.2, C66.1, C68.2, Q9.3 (S), Q11.3 (S), Q13.3 (S), R45.2, R48.2, R51.2, R57.2, R59.2, R63.2, U14.2 (V-), U15.4 (GND), U16.2 (V-), U17.4 (GND), U18.2 (V-), U19.4 (GND); also elsewhere on the board
MOTOR2_BEMF_U: J12.1, JP4.2 (C); also elsewhere on the board
MOTOR2_BEMF_V: J12.4, JP5.2 (C); also elsewhere on the board
MOTOR2_BEMF_W: J12.7, JP6.2 (C); also elsewhere on the board
MOTOR2_PWM_UH: J12.2, U15.2 (INH); also elsewhere on the board
MOTOR2_PWM_UL: J12.3, U15.3 (INL); also elsewhere on the board
MOTOR2_PWM_VH: J12.5, U17.2 (INH); also elsewhere on the board
MOTOR2_PWM_VL: J12.6, U17.3 (INL); also elsewhere on the board
MOTOR2_PWM_WH: J12.8, U19.2 (INH); also elsewhere on the board
MOTOR2_PWM_WL: J12.9, U19.3 (INL); also elsewhere on the board
unnamed: JP4.1 (A), U14.1
unnamed: JP5.1 (A), U16.1
unnamed: JP6.1 (A), U18.1
unnamed: Q8.1 (G), R44.2, R46.1
unnamed: Q9.1 (G), R47.2, R48.1
unnamed: Q10.1 (G), R53.2, R55.1
unnamed: Q11.1 (G), R56.2, R57.1
unnamed: Q12.1 (G), R60.2, R61.1
unnamed: Q13.1 (G), R62.2, R63.1
unnamed: C56.1, U15.8 (BST)
unnamed: R44.1, U15.7 (GH)
unnamed: R47.1, U15.5 (GL)
unnamed: C62.1, U17.8 (BST)
unnamed: R53.1, U17.7 (GH)
unnamed: R56.1, U17.5 (GL)
unnamed: C67.1, U19.8 (BST)
unnamed: R60.1, U19.7 (GH)
unnamed: R62.1, U19.5 (GL)
VBUS: C54.2, C58.1, C60.2, C63.1, C66.2, C68.1, Q8.2 (D), Q10.2 (D), Q12.2 (D), U15.1 (GVDD), U17.1 (GVDD), U19.1 (GVDD); also elsewhere on the board

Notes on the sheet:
MOTOR 2 BEMF signals conditioning
MOTOR 2 triple half-bridge

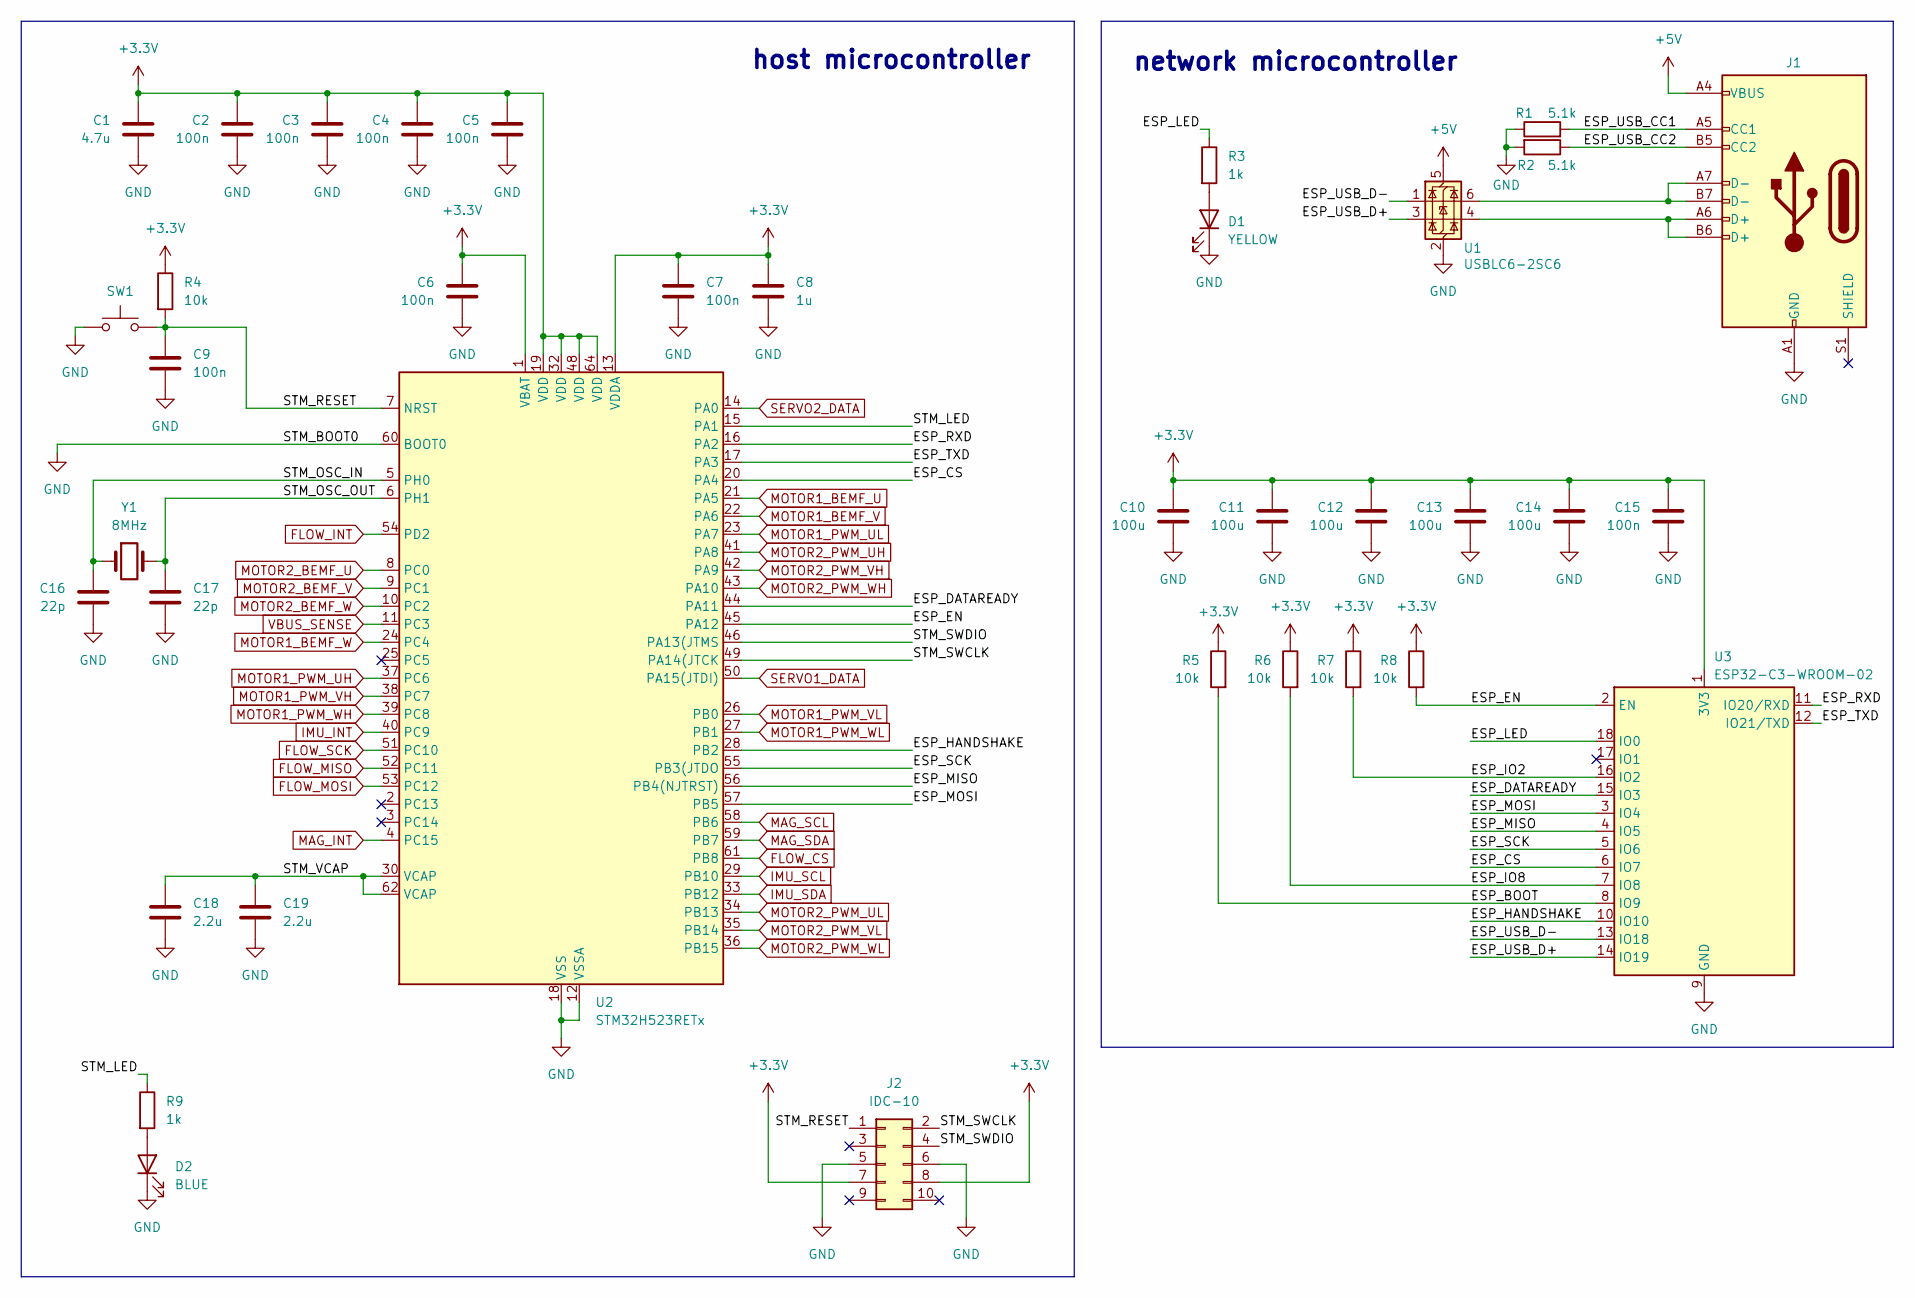
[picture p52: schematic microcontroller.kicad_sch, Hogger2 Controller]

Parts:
C1: 4.7u; C_0603_1608Metric
C2, C3, C4, C5, C6, C7, C9, C15: 100n; C_0603_1608Metric
C8: 1u; C_0603_1608Metric
C10, C11, C12, C13, C14: 100u; C_1206_3216Metric
C16, C17: 22p; C_0603_1608Metric
C18, C19: 2.2u; C_0603_1608Metric
D1: YELLOW; LED_0603_1608Metric
D2: BLUE; LED_0603_1608Metric
J1: USB_C_Receptacle_USB2.0_14P; USB_C_Receptacle_GCT_USB4085
J2: IDC-10; IDC-Header_2x05_P2.54mm_Vertical
R1, R2: 5.1k; R_0603_1608Metric
R3, R9: 1k; R_0603_1608Metric
R4, R5, R6, R7, R8: 10k; R_0603_1608Metric
SW1: SW_Push; spst_6x3mm
U1: USBLC6-2SC6; SOT-23-6
U2: STM32H523RETx; LQFP-64_10x10mm_P0.5mm
U3: ESP32-C3-WROOM-02
Y1: 8MHz; Crystal_SMD_5032-2Pin_5.0x3.2mm

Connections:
+3.3V: C1.1, C2.1, C3.1, C4.1, C5.1, C6.1, C7.1, C8.1, C10.1, C11.1, C12.1, C13.1, C14.1, C15.1, J2.7, J2.8, R4.1, R5.1, R6.1, R7.1, R8.1, U2.1 (VBAT), U2.13 (VDDA), U2.19 (VDD), U2.32 (VDD), U2.48 (VDD), U2.64 (VDD), U3.1 (3V3); also elsewhere on the board
+5V: J1.A4 (VBUS), J1.A9 (VBUS), J1.B4 (VBUS), J1.B9 (VBUS), U1.5 (VBUS); also elsewhere on the board
/microcontroller/ESP_BOOT: R5.2, U3.8 (IO9)
/microcontroller/ESP_CS: U2.20 (PA4), U3.6 (IO7)
/microcontroller/ESP_EN: R8.2, U2.45 (PA12), U3.2 (EN)
/microcontroller/ESP_HANDSHAKE: U2.44 (PA11), U3.15 (IO3)
/microcontroller/ESP_IO2: R7.2, U3.16 (IO2)
/microcontroller/ESP_IO8: R6.2, U3.7 (IO8)
/microcontroller/ESP_LED: R3.1, U3.18 (IO0)
/microcontroller/ESP_MISO: U2.56 (PB4(NJTRST)), U3.4 (IO5)
/microcontroller/ESP_MOSI: U2.57 (PB5), U3.3 (IO4)
/microcontroller/ESP_RDY: U2.28 (PB2), U3.10 (IO10)
/microcontroller/ESP_RXD: U2.16 (PA2), U3.11 (IO20/RXD)
/microcontroller/ESP_SCK: U2.55 (PB3(JTDO), U3.5 (IO6)
/microcontroller/ESP_TXD: U2.17 (PA3), U3.12 (IO21/TXD)
/microcontroller/ESP_USB_CC1: J1.A5 (CC1), R1.2
/microcontroller/ESP_USB_CC2: J1.B5 (CC2), R2.1
/microcontroller/ESP_USB_D+: U1.3 (I/O2), U3.14 (IO19)
/microcontroller/ESP_USB_D-: U1.1 (I/O1), U3.13 (IO18)
/microcontroller/STM_LED: R9.1, U2.15 (PA1)
/microcontroller/STM_OSC_IN: C16.1, U2.5 (PH0), Y1.1
/microcontroller/STM_OSC_OUT: C17.1, U2.6 (PH1), Y1.2
/microcontroller/STM_RESET: C9.1, J2.1, R4.2, SW1.2, U2.7 (NRST)
/microcontroller/STM_SWCLK: J2.2, U2.49 (PA14(JTCK)
/microcontroller/STM_SWDIO: J2.4, U2.46 (PA13(JTMS)
/microcontroller/STM_VCAP: C18.1, C19.1, U2.30 (VCAP), U2.62 (VCAP)
FLOW_CS: U2.61 (PB8); also elsewhere on the board
FLOW_INT: U2.54 (PD2); also elsewhere on the board
FLOW_MISO: U2.52 (PC11); also elsewhere on the board
FLOW_MOSI: U2.53 (PC12); also elsewhere on the board
FLOW_SCK: U2.51 (PC10); also elsewhere on the board
GND: C1.2, C2.2, C3.2, C4.2, C5.2, C6.2, C7.2, C8.2, C9.2, C10.2, C11.2, C12.2, C13.2, C14.2, C15.2, C16.2, C17.2, C18.2, C19.2, D1.1 (K), D2.1 (K), J1.A1 (GND), J1.A12 (GND), J1.B1 (GND), J1.B12 (GND), J2.5, J2.6, R1.1, R2.2, SW1.1, U1.2 (GND), U2.12 (VSSA), U2.18 (VSS), U2.31 (VSS), U2.47 (VSS), U2.60 (BOOT0), U2.63 (VSS), U3.9 (GND), U3.19 (GND); also elsewhere on the board
IMU_INT: U2.40 (PC9); also elsewhere on the board
IMU_SCL: U2.29 (PB10); also elsewhere on the board
IMU_SDA: U2.33 (PB12); also elsewhere on the board
MAG_INT: U2.4 (PC15); also elsewhere on the board
MAG_SCL: U2.58 (PB6); also elsewhere on the board
MAG_SDA: U2.59 (PB7); also elsewhere on the board
MOTOR1_BEMF_U: U2.21 (PA5); also elsewhere on the board
MOTOR1_BEMF_V: U2.22 (PA6); also elsewhere on the board
MOTOR1_BEMF_W: U2.24 (PC4); also elsewhere on the board
MOTOR1_PWM_UH: U2.37 (PC6); also elsewhere on the board
MOTOR1_PWM_UL: U2.23 (PA7); also elsewhere on the board
MOTOR1_PWM_VH: U2.38 (PC7); also elsewhere on the board
MOTOR1_PWM_VL: U2.26 (PB0); also elsewhere on the board
MOTOR1_PWM_WH: U2.39 (PC8); also elsewhere on the board
MOTOR1_PWM_WL: U2.27 (PB1); also elsewhere on the board
MOTOR2_BEMF_U: U2.8 (PC0); also elsewhere on the board
MOTOR2_BEMF_V: U2.9 (PC1); also elsewhere on the board
MOTOR2_BEMF_W: U2.10 (PC2); also elsewhere on the board
MOTOR2_PWM_UH: U2.41 (PA8); also elsewhere on the board
MOTOR2_PWM_UL: U2.34 (PB13); also elsewhere on the board
MOTOR2_PWM_VH: U2.42 (PA9); also elsewhere on the board
MOTOR2_PWM_VL: U2.35 (PB14); also elsewhere on the board
MOTOR2_PWM_WH: U2.43 (PA10); also elsewhere on the board
MOTOR2_PWM_WL: U2.36 (PB15); also elsewhere on the board
unnamed: D1.2 (A), R3.2
unnamed: D2.2 (A), R9.2
unnamed: J1.A6 (D+), J1.B6 (D+), U1.4 (I/O2)
unnamed: J1.A7 (D-), J1.B7 (D-), U1.6 (I/O1)
SERVO1_DATA: U2.50 (PA15(JTDI)); also elsewhere on the board
SERVO2_DATA: U2.14 (PA0); also elsewhere on the board
VBUS_SENSE: U2.11 (PC3); also elsewhere on the board

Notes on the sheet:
network microcontroller
host microcontroller

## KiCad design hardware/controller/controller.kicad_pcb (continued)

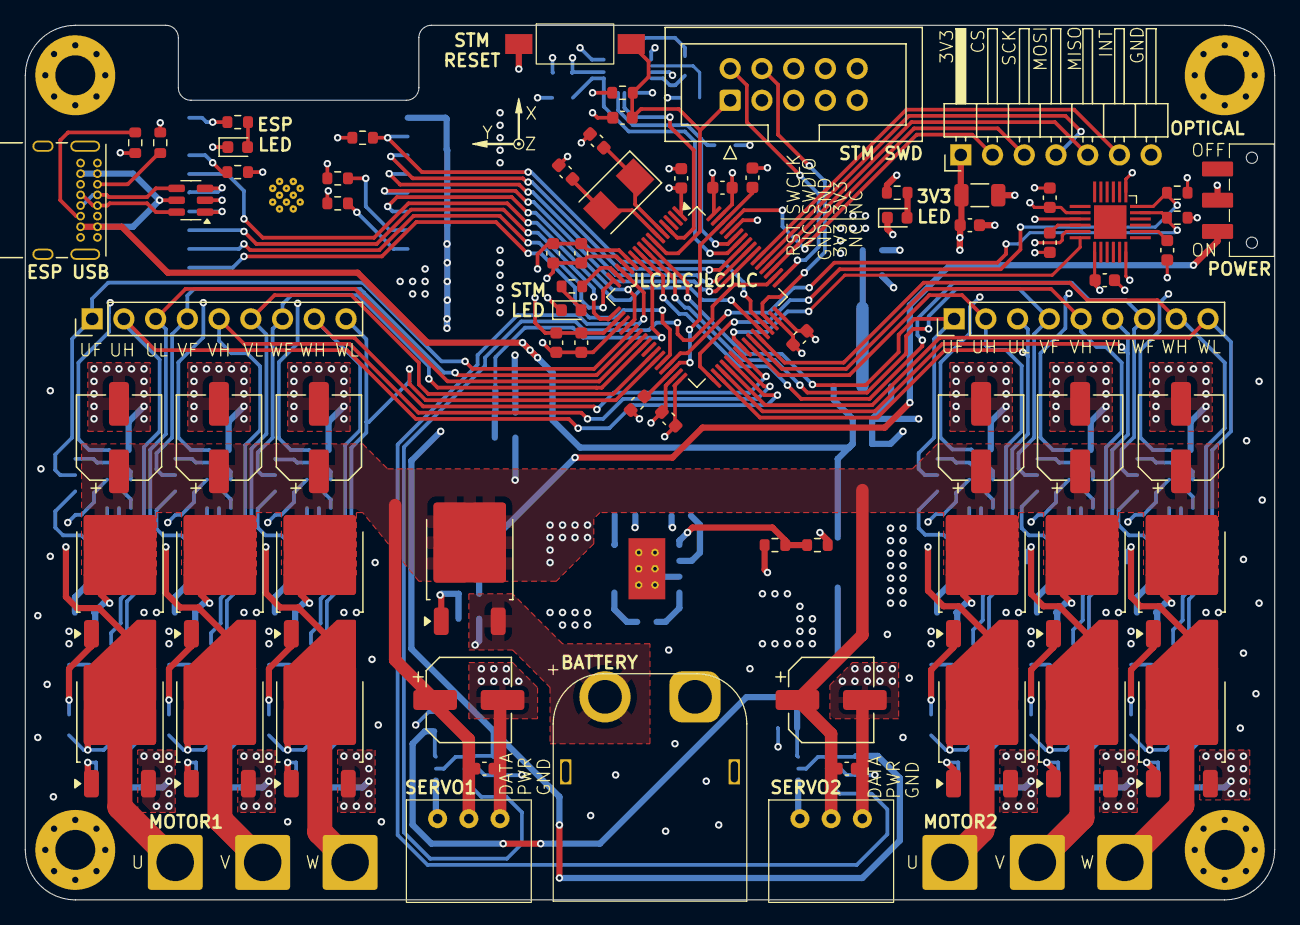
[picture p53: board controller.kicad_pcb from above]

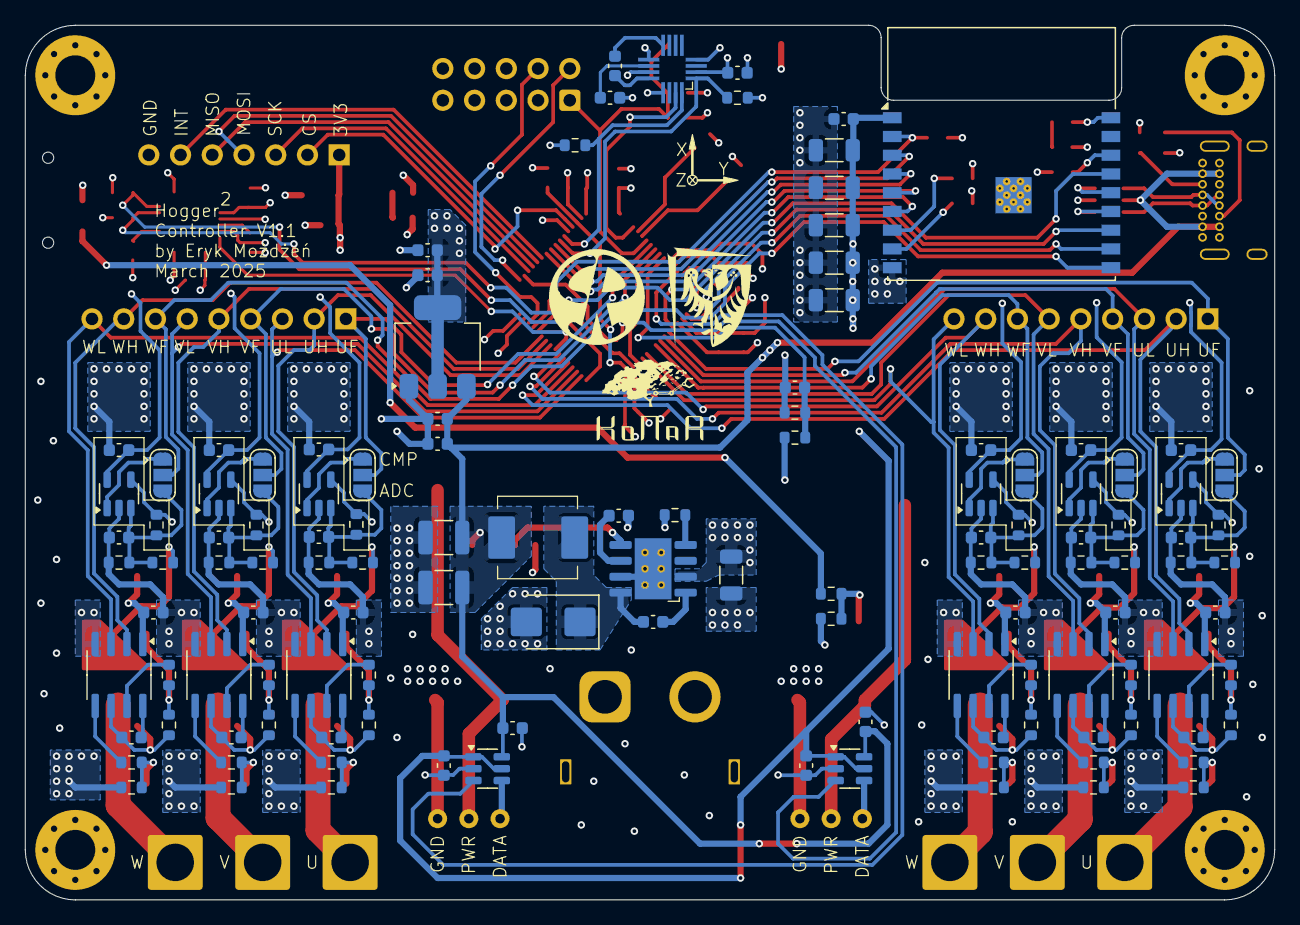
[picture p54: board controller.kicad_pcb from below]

Board: 4 copper layers, 100.0 x 70.0 mm, 205 parts (122 on the bottom side), 130 nets.

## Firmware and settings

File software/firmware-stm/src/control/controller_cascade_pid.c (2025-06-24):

#include <math.h>

#include "actuate/servos.h"
#include "com/stream.h"
#include "com/telemetry.h"
#include "control/pid.h"
#include "control/robot_parameters.h"
#include "control/trajectory.h"
#include "control/watchdog.h"
#include "generated/estimator.h"
#include "utils/task.h"

#define MOTOR_VEL -250.f

// #define EXPERIMENT_INNER_THETA
// #define EXPERIMENT_OUTER_THETA
// #define EXPERIMENT_INNER_X
// #define EXPERIMENT_INNER_Y
// #define EXPERIMENT_OUTER_X
// #define EXPERIMENT_OUTER_Y

typedef struct {
    bool started;
    uint32_t time_start;
    float time;

    float exp_step;
    float exp_response;

    pid_t inner_x;
    pid_t inner_y;
    pid_t inner_theta;

    pid_t outer_x;
    pid_t outer_y;
    pid_t outer_theta;
} controller_t;

static controller_t controller = {
    .inner_theta = PID_INIT(2.260574, 3.511004, 0, -4 * M_PI, 4 * M_PI), // PI CHR 0%
    .outer_theta = PID_INIT(11.334450, 0, 3.838592, -M_PI, M_PI),        // PD Lambda = 0.25
    .inner_x = PID_INIT(3.726573, 5.949067, 0, -1.5, 1.5),               // PI CHR 0%
    .inner_y = PID_INIT(0.816472, 1.703120, 0, -1.5, 1.5),               // PI CHR 0%
    .outer_x = PID_INIT(4.257331, 0, 1.104396, -0.5, 0.5),               // PD Lambda = 1
    .outer_y = PID_INIT(3.626742, 0, 1.073429, -0.5, 0.5),               // PD Lambda = 1
};

static void Tu(const float u_x, const float u_y, const float u_theta, float *output) {
    output[0] = -u_x / (ROBOT_PARAMETER_R * MOTOR_VEL);
    output[1] = -u_y / (ROBOT_PARAMETER_R * MOTOR_VEL);
    output[2] = (u_x / (ROBOT_PARAMETER_R * MOTOR_VEL)) +
                ((2 * ROBOT_PARAMETER_L * u_theta) / (ROBOT_PARAMETER_R * MOTOR_VEL));
    output[3] = u_y / (ROBOT_PARAMETER_R * MOTOR_VEL);
}

static void Ttheta(const float theta, const float x, const float y, float *output) {
    const float sin_theta = sinf(theta);
    const float cos_theta = cosf(theta);

    output[0] = +(x * cos_theta) + (y * sin_theta);
    output[1] = -(x * sin_theta) + (y * cos_theta);
}

static void ok(mpack_t *mpack) {
    (void)mpack;

    watchdog_reset();

    if(!controller.started) {
        controller.started = true;
        controller.time_start = task_timebase();

        pid_reset(&controller.inner_x);
        pid_reset(&controller.inner_y);
        pid_reset(&controller.inner_theta);

        pid_reset(&controller.outer_x);
        pid_reset(&controller.outer_y);
        pid_reset(&controller.outer_theta);
    }
}

static void abort() {
    controller.started = false;
}

static void loop() {
    const uint32_t now = task_timebase();

    controller.time = (now - controller.time_start) * 0.000001f;

    if(!controller.started) {
        return;
    }

    trajectory_t trajectory;
    trajectory_get(&trajectory, controller.time);

    const float theta = estimator_state_get_theta();
    const float dtheta = estimator_state_get_dottheta();

    float local_pos_ref[2];
    Ttheta(theta, TRAJECTORY_GET_X(&trajectory), TRAJECTORY_GET_Y(&trajectory), local_pos_ref);

    float local_vel_ref[2];
    Ttheta(theta, TRAJECTORY_GET_D_X(&trajectory), TRAJECTORY_GET_D_Y(&trajectory), local_vel_ref);

    float local_pos[2];
    Ttheta(theta, estimator_state_get_x(), estimator_state_get_y(), local_pos);

    float local_vel[2];
    Ttheta(theta, estimator_state_get_dotx(), estimator_state_get_doty(), local_vel);

#if !defined(EXPERIMENT_INNER_THETA) && !defined(EXPERIMENT_INNER_X) &&                            \
    !defined(EXPERIMENT_INNER_Y) && !defined(EXPERIMENT_OUTER_THETA) &&                            \
    !defined(EXPERIMENT_OUTER_X) && !defined(EXPERIMENT_OUTER_Y)
    const float vel_x = pid_calculate(&controller.outer_x, local_pos_ref[0], local_pos[0]);
    const float vel_y = pid_calculate(&controller.outer_y, local_pos_ref[1], local_pos[1]);
    const float vel_theta =
        pid_calculate(&controller.outer_theta, TRAJECTORY_GET_THETA(&trajectory), theta);

    const float inner_vel_ref_x = local_vel_ref[0] + vel_x;
    const float inner_vel_ref_y = local_vel_ref[1] + vel_y;
    const float inner_vel_ref_theta = TRAJECTORY_GET_D_THETA(&trajectory) + vel_theta;

    const float u_x = pid_calculate(&controller.inner_x, inner_vel_ref_x, local_vel[0]);
    const float u_y = pid_calculate(&controller.inner_y, inner_vel_ref_y, local_vel[1]);
    const float u_theta = pid_calculate(&controller.inner_theta, inner_vel_ref_theta, dtheta);
#endif

#ifdef EXPERIMENT_INNER_THETA
    controller.exp_step = (controller.time > 3) ? 2 : 0;
    controller.exp_response = dtheta;

    const float u_x = 0;
    const float u_y = 0;
    const float u_theta = controller.exp_step;
#endif

#ifdef EXPERIMENT_OUTER_THETA
    controller.exp_step = (controller.time > 3) ? 2 : 0;
    controller.exp_response = theta;

    const float u_x = 0;
    const float u_y = 0;
    const float u_theta = pid_calculate(&controller.inner_theta, controller.exp_step, dtheta);
#endif

#ifdef EXPERIMENT_INNER_X
    controller.exp_step = (controller.time > 3) ? 0.5f : 0;
    controller.exp_response = local_vel[0];

    const float vel_theta = pid_calculate(&controller.outer_theta, 0, theta);

    const float u_x = controller.exp_step;
    const float u_y = 0;
    const float u_theta = pid_calculate(&controller.inner_theta, vel_theta, dtheta);
#endif

#ifdef EXPERIMENT_INNER_Y
    controller.exp_step = (controller.time > 3) ? 0.5f : 0;
    controller.exp_response = local_vel[1];

    const float vel_theta = pid_calculate(&controller.outer_theta, 0, theta);

    const float u_x = 0;
    const float u_y = controller.exp_step;
    const float u_theta = pid_calculate(&controller.inner_theta, vel_theta, dtheta);
#endif

#ifdef EXPERIMENT_OUTER_X
    controller.exp_step = (controller.time > 5) ? 0.5f : 0;
    controller.exp_response = local_pos[0];

    const float vel_theta = pid_calculate(&controller.outer_theta, 0, theta);

    const float u_x = pid_calculate(&controller.inner_x, controller.exp_step, local_vel[0]);
    const float u_y = pid_calculate(&controller.inner_y, 0, local_vel[1]);
    const float u_theta = pid_calculate(&controller.inner_theta, vel_theta, dtheta);
#endif

#ifdef EXPERIMENT_OUTER_Y
    controller.exp_step = (controller.time > 5) ? 0.5f : 0;
    controller.exp_response = local_pos[1];

    const float vel_theta = pid_calculate(&controller.outer_theta, 0, theta);

    const float u_x = pid_calculate(&controller.inner_x, 0, local_vel[0]);
    const float u_y = pid_calculate(&controller.inner_y, controller.exp_step, local_vel[1]);
    const float u_theta = pid_calculate(&controller.inner_theta, vel_theta, dtheta);
#endif

    float angles[4];
    Tu(u_x, u_y, u_theta, angles);

    servos_set_position(angles[0], angles[1], angles[2], angles[3]);
}

static void serialize(cmp_ctx_t *cmp, void *context) {
    (void)context;

    cmp_write_map(cmp, 3);
    cmp_write_str(cmp, "started", 7);
    cmp_write_bool(cmp, controller.started);

    cmp_write_str(cmp, "exp_step", 8);
    cmp_write_float(cmp, controller.exp_step);

    cmp_write_str(cmp, "exp_response", 12);
    cmp_write_float(cmp, controller.exp_response);
}

STREAM_REGISTER("controller_continue", ok)
WATCHDOG_REGISTER(abort)
TASK_REGISTER_PERIODIC(loop, 1000)
TELEMETRY_REGISTER("controller", serialize, NULL)

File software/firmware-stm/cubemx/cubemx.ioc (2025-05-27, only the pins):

Mcu.UserName=STM32H523RETx
PA0.GPIO_Label=SERVO2_DATA
PA0.Signal=UART4_TX
PA1.GPIO_Label=LED
PA1.Signal=GPIO_Output
PA10.GPIO_Label=MOTOR2_PWM_WH
PA10.Signal=S_TIM1_CH3
PA12.GPIO_Label=ESP_EN
PA12.Signal=GPIO_Output
PA15(JTDI).GPIO_Label=SERVO1_DATA
PA15(JTDI).Signal=USART1_TX
PA4.GPIO_Label=ESP_CS
PA4.Signal=GPIO_Output
PA5.GPIO_Label=MOTOR1_BEMF_U
PA5.Signal=ADCx_INP19
PA6.GPIO_Label=MOTOR1_BEMF_V
PA6.Signal=ADCx_INP3
PA7.GPIO_Label=MOTOR1_PWM_UL
PA7.Signal=TIM8_CH1N
PA8.GPIO_Label=MOTOR2_PWM_UH
PA8.Signal=S_TIM1_CH1
PA9.GPIO_Label=MOTOR2_PWM_VH
PA9.Signal=S_TIM1_CH2
PB0.GPIO_Label=MOTOR1_PWM_VL
PB0.Signal=TIM8_CH2N
PB1.GPIO_Label=MOTOR1_PWM_WL
PB1.Signal=TIM8_CH3N
PB10.GPIO_Label=IMU_SCL
PB10.Signal=I2C2_SCL
PB12.GPIO_Label=IMU_SDA
PB12.Signal=I2C2_SDA
PB13.GPIO_Label=MOTOR2_PWM_UL
PB13.Signal=TIM1_CH1N
PB14.GPIO_Label=MOTOR2_PWM_VL
PB14.Signal=TIM1_CH2N
PB15.GPIO_Label=MOTOR2_PWM_WL
PB15.Signal=TIM1_CH3N
PB2.GPIO_Label=ESP_HANDSHAKE
PB2.Signal=GPXTI2
PB3(JTDO/TRACESWO).GPIO_Label=ESP_SCK
PB3(JTDO/TRACESWO).Signal=SPI1_SCK
PB4(NJTRST).GPIO_Label=ESP_MISO
PB4(NJTRST).Signal=SPI1_MISO
PB5.GPIO_Label=ESP_MOSI
PB5.Signal=SPI1_MOSI
PB6.GPIO_Label=MAG_SCL
PB6.Signal=I2C1_SCL
PB7.GPIO_Label=MAG_SDA
PB7.Signal=I2C1_SDA
PB8.GPIO_Label=FLOW_CS
PB8.Signal=GPIO_Output
PC0.GPIO_Label=MOTOR2_BEMF_U
PC0.Signal=ADCx_INP10
PC1.GPIO_Label=MOTOR2_BEMF_V
PC1.Signal=ADCx_INP11
PC10.GPIO_Label=FLOW_SCK
PC10.Signal=SPI3_SCK
PC11.GPIO_Label=FLOW_MISO
PC11.Signal=SPI3_MISO
PC12.GPIO_Label=FLOW_MOSI
PC12.Signal=SPI3_MOSI
PC15-OSC32_OUT(OSC32_OUT).GPIO_Label=MAG_INT
PC15-OSC32_OUT(OSC32_OUT).Signal=GPXTI15
PC2.GPIO_Label=MOTOR2_BEMF_W
PC2.Signal=ADCx_INP12
PC3.GPIO_Label=VBUS_SENSE
PC3.Signal=ADCx_INP13
PC4.GPIO_Label=MOTOR1_BEMF_W
PC4.Signal=ADCx_INP4
PC6.GPIO_Label=MOTOR1_PWM_UH
PC6.Signal=S_TIM8_CH1
PC7.GPIO_Label=MOTOR1_PWM_VH
PC7.Signal=S_TIM8_CH2
PC8.GPIO_Label=MOTOR1_PWM_WH
PC8.Signal=S_TIM8_CH3
PC9.GPIO_Label=IMU_INT
PC9.Signal=GPXTI9
PH0-OSC_IN(PH0).Signal=RCC_OSC_IN
PH1-OSC_OUT(PH1).Signal=RCC_OSC_OUT

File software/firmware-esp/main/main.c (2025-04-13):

#include <cmp/cmp.h>
#include <driver/gpio.h>
#include <driver/spi_slave.h>
#include <esp_log.h>
#include <esp_wifi.h>
#include <freertos/FreeRTOS.h>
#include <freertos/semphr.h>
#include <freertos/task.h>
#include <lrcp/frame.h>
#include <lrcp/stream.h>
#include <netdb.h>
#include <nvs_flash.h>
#include <stdio.h>
#include <string.h>
#include <sys/socket.h>

#define GPIO_LED       0
#define GPIO_MOSI      4
#define GPIO_MISO      5
#define GPIO_SCK       6
#define GPIO_CS        7
#define GPIO_HANDSHAKE 10

#define WIFI_SSID     "Hogger^2"
#define WIFI_PASSWORD "12345678"
#define RX_PORT       3333
#define TX_PORT       4444
#define BUFFER_SIZE   (32 * 1024)

#define SPI_TRANSACTION_SIZE 2048
#define SPI_HEADER_SIZE      sizeof(uint16_t)
#define SPI_PAYLOAD_SIZE     (SPI_TRANSACTION_SIZE - SPI_HEADER_SIZE)

typedef struct {
    uint8_t rx_buffer[SPI_TRANSACTION_SIZE];
    uint8_t tx_buffer[SPI_TRANSACTION_SIZE];

    uint16_t rx_size;
    uint16_t tx_size;

    lrcp_stream_t base;
    QueueHandle_t rx_queue;
    QueueHandle_t tx_queue;
    SemaphoreHandle_t lock;
} spi_t;

typedef struct {
    uint8_t *buffer;
    size_t capacity;
    size_t size;
    size_t position;
} cmp_buffer_t;

static spi_t spi;

static void spi_transaction_setup(spi_slave_transaction_t *transaction) {
    (void)transaction;

    BaseType_t mustYield = pdFALSE;

    for(spi.tx_size = 0; spi.tx_size < SPI_PAYLOAD_SIZE; spi.tx_size++) {
        if(!xQueueReceiveFromISR(spi.tx_queue, &spi.tx_buffer[SPI_HEADER_SIZE + spi.tx_size],
                                 &mustYield)) {
            break;
        }
    }

    memcpy(spi.tx_buffer, &spi.tx_size, SPI_HEADER_SIZE);

    gpio_set_level(GPIO_HANDSHAKE, 1);

    if(mustYield) {
        portYIELD_FROM_ISR();
    }
}

static void spi_transaction_end(spi_slave_transaction_t *transaction) {
    (void)transaction;

    memcpy(&spi.rx_size, spi.rx_buffer, SPI_HEADER_SIZE);

    if(spi.rx_size > SPI_PAYLOAD_SIZE) {
        spi.rx_size = SPI_PAYLOAD_SIZE;
    }

    BaseType_t mustYield = pdFALSE;

    for(uint32_t i = 0; i < spi.rx_size; i++) {
        xQueueSendFromISR(spi.rx_queue, &spi.rx_buffer[SPI_HEADER_SIZE + i], &mustYield);
    }

    gpio_set_level(GPIO_HANDSHAKE, 0);

    if(mustYield) {
        portYIELD_FROM_ISR();
    }
}

static uint32_t spi_stream_reader(void *context, void *data, const uint32_t data_capacity) {
    (void)context;

    for(uint32_t i = 0; i < data_capacity; i++) {
        if(!xQueueReceive(spi.rx_queue, &((uint8_t *)data)[i], 0)) {
            return i;
        }
    }

    return data_capacity;
}

static uint32_t spi_stream_writer(void *context, const void *data, const uint32_t data_size) {
    (void)context;

    for(uint32_t i = 0; i < data_size; i++) {
        if(!xQueueSend(spi.tx_queue, &((uint8_t *)data)[i], 0)) {
            return i;
        }
    }

    return data_size;
}

static void spi_task(void *arg) {
    ESP_LOGI("app", "SPI task started");

    spi_slave_transaction_t transaction = {
        .length = SPI_TRANSACTION_SIZE * 8,
        .tx_buffer = &spi.tx_buffer,
        .rx_buffer = &spi.rx_buffer,
    };

    while(1) {
        spi_slave_transmit(SPI2_HOST, &transaction, portMAX_DELAY);
    }
}

static void spi_init() {
    lrcp_stream_init(&spi.base, NULL, spi_stream_reader, spi_stream_writer);

    spi.rx_queue = xQueueCreate(BUFFER_SIZE, 1);
    spi.tx_queue = xQueueCreate(BUFFER_SIZE, 1);
    spi.lock = xSemaphoreCreateMutex();

    const spi_bus_config_t buscfg = {
        .mosi_io_num = GPIO_MOSI,
        .miso_io_num = GPIO_MISO,
        .sclk_io_num = GPIO_SCK,
        .quadwp_io_num = -1,
        .quadhd_io_num = -1,
        .max_transfer_sz = SPI_TRANSACTION_SIZE,
    };

    const spi_slave_interface_config_t slvcfg = {
        .mode = 0,
        .spics_io_num = GPIO_CS,
        .queue_size = 8,
        .flags = 0,
        .post_setup_cb = spi_transaction_setup,
        .post_trans_cb = spi_transaction_end,
    };

    const gpio_config_t gpiocfg = {
        .pin_bit_mask = BIT64(GPIO_HANDSHAKE),
        .mode = GPIO_MODE_OUTPUT,
    };

    spi_slave_initialize(SPI2_HOST, &buscfg, &slvcfg, SPI_DMA_CH_AUTO);
    gpio_config(&gpiocfg);
}

static size_t cmp_buffer_writer(cmp_ctx_t *ctx, const void *data, size_t count) {
    cmp_buffer_t *buf = (cmp_buffer_t *)ctx->buf;

    if((buf->position + count) > buf->capacity) {
        return 0;
    }

    memcpy(buf->buffer + buf->position, data, count);
    buf->position += count;
    buf->size = buf->position;

    return count;
}

static void wifi_transmitter_task(void *params) {
    (void)params;

    const int sock = socket(AF_INET, SOCK_DGRAM, IPPROTO_IP);

    int broadcast = 1;
    setsockopt(sock, SOL_SOCKET, SO_BROADCAST, &broadcast, sizeof(broadcast));

    esp_netif_ip_info_t ip_info;
    esp_netif_t *netif_sta = esp_netif_get_handle_from_ifkey("WIFI_STA_DEF");
    esp_netif_get_ip_info(netif_sta, &ip_info);

    static uint8_t decoded[BUFFER_SIZE];
    lrcp_decoder_t decoder;
    lrcp_frame_decoder_init(&decoder);

    struct sockaddr_in dest_addr = {
        .sin_family = AF_INET,
        .sin_port = htons(TX_PORT),
        .sin_addr.s_addr = (ip_info.ip.addr & ip_info.netmask.addr) | (~ip_info.netmask.addr),
    };

    uint32_t last = xTaskGetTickCount();

    ESP_LOGI("app", "WIFI transmitter started on port %d", TX_PORT);

    while(1) {
        uint32_t size;

        do {
            xSemaphoreTake(spi.lock, portMAX_DELAY);
            size = lrcp_frame_decode(&spi.base, &decoder, decoded, sizeof(decoded));
            xSemaphoreGive(spi.lock);

            if(size > 0) {
                last = xTaskGetTickCount();
                sendto(sock, decoded, size, 0, (struct sockaddr *)&dest_addr, sizeof(dest_addr));
            }
        } while(size);

        if((xTaskGetTickCount() - last) >= 100) {
            last = xTaskGetTickCount();

            uint8_t buf[128];

            cmp_buffer_t buffer = {
                .buffer = buf,
                .capacity = sizeof(buf),
                .size = 0,
                .position = 0,
            };
            cmp_ctx_t cmp;
            cmp_init(&cmp, &buffer, NULL, NULL, cmp_buffer_writer);

            cmp_write_map(&cmp, 1);
            cmp_write_str(&cmp, "host_timeout", 12);
            cmp_write_nil(&cmp);

            sendto(sock, buffer.buffer, buffer.size, 0, (struct sockaddr *)&dest_addr,
                   sizeof(dest_addr));
        }

        vTaskDelay(1);
    }
}
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

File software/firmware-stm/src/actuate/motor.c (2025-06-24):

#include <math.h>
#include <stdbool.h>
#include <stdint.h>
#include <stm32h5xx_hal.h>

#include "actuate/motor.h"
#include "control/pid.h"

#define POLE_PAIRS    7
#define VEL_THRESHOLD 50.f
#define VEL_PERIOD    20
#define VEL_FILTER    0.9f

#define ALIGN_TIME  200
#define ALIGN_PULSE 0.3f

#define OPEN_LOOP_PULSE       0.4f
#define OPEN_LOOP_RAMP_TIME   1000
#define OPEN_LOOP_RAMP_LAMBDA 1.f
#define OPEN_LOOP_RAMP_MIN    1000
#define OPEN_LOOP_RAMP_MAX    200000

#define CLOSED_LOOP_SWITCH 1000

// #define EXPERIMENT

#define CLAMP(val, min, max) (((val) > (max)) ? (max) : (((val) < (min)) ? (min) : (val)))

#ifndef EXPERIMENT
#define INCREMENT(motor, val) ((val >= 0) ^ (motor)->reverse_direction)
#else
#define INCREMENT(motor, val) 0
#endif

static const motor_phase_t feedback_src_lookup_inc[6] = {
    MOTOR_PHASE_U, MOTOR_PHASE_W, MOTOR_PHASE_V, MOTOR_PHASE_U, MOTOR_PHASE_W, MOTOR_PHASE_V,
};

static const motor_phase_t feedback_src_lookup_dec[6] = {
    MOTOR_PHASE_V, MOTOR_PHASE_U, MOTOR_PHASE_W, MOTOR_PHASE_V, MOTOR_PHASE_U, MOTOR_PHASE_W,
};

static const uint8_t feedback_dir_lookup[6] = {
    0, 1, 0, 1, 0, 1,
};

static const uint8_t filter_lookup[256] = {
    0, 1, 1, 2, 1, 2, 2, 3, 1, 2, 2, 3, 2, 3, 3, 4, 1, 2, 2, 3, 2, 3, 3, 4, 2, 3, 3, 4, 3, 4, 4, 5,
    1, 2, 2, 3, 2, 3, 3, 4, 2, 3, 3, 4, 3, 4, 4, 5, 2, 3, 3, 4, 3, 4, 4, 5, 3, 4, 4, 5, 4, 5, 5, 6,
    1, 2, 2, 3, 2, 3, 3, 4, 2, 3, 3, 4, 3, 4, 4, 5, 2, 3, 3, 4, 3, 4, 4, 5, 3, 4, 4, 5, 4, 5, 5, 6,
    2, 3, 3, 4, 3, 4, 4, 5, 3, 4, 4, 5, 4, 5, 5, 6, 3, 4, 4, 5, 4, 5, 5, 6, 4, 5, 5, 6, 5, 6, 6, 7,
    1, 2, 2, 3, 2, 3, 3, 4, 2, 3, 3, 4, 3, 4, 4, 5, 2, 3, 3, 4, 3, 4, 4, 5, 3, 4, 4, 5, 4, 5, 5, 6,
    2, 3, 3, 4, 3, 4, 4, 5, 3, 4, 4, 5, 4, 5, 5, 6, 3, 4, 4, 5, 4, 5, 5, 6, 4, 5, 5, 6, 5, 6, 6, 7,
    2, 3, 3, 4, 3, 4, 4, 5, 3, 4, 4, 5, 4, 5, 5, 6, 3, 4, 4, 5, 4, 5, 5, 6, 4, 5, 5, 6, 5, 6, 6, 7,
    3, 4, 4, 5, 4, 5, 5, 6, 4, 5, 5, 6, 5, 6, 6, 7, 4, 5, 5, 6, 5, 6, 6, 7, 5, 6, 6, 7, 6, 7, 7, 8,
};

static void config_pwm(const motor_t *motor, const uint32_t channel) {
    const uint32_t pulse = motor->pulse * motor->control_timer->Instance->ARR;

    HAL_TIM_OC_Stop(motor->control_timer, channel);
    HAL_TIM_PWM_Stop(motor->control_timer, channel);
    HAL_TIMEx_OCN_Stop(motor->control_timer, channel);
    HAL_TIMEx_PWMN_Stop(motor->control_timer, channel);

    const TIM_OC_InitTypeDef config = {
        .OCMode = TIM_OCMODE_PWM1,
        .Pulse = pulse,
        .OCPolarity = TIM_OCPOLARITY_HIGH,
        .OCNPolarity = TIM_OCNPOLARITY_HIGH,
        .OCFastMode = TIM_OCFAST_DISABLE,
        .OCIdleState = TIM_OCIDLESTATE_RESET,
        .OCNIdleState = TIM_OCNIDLESTATE_RESET,
    };
    HAL_TIM_PWM_ConfigChannel(motor->control_timer, &config, channel);

    HAL_TIM_PWM_Start(motor->control_timer, channel);
    HAL_TIMEx_PWMN_Start(motor->control_timer, channel);
}

static void config_oc(const motor_t *motor, const uint32_t channel, const uint32_t mode) {
    const uint32_t pulse = motor->pulse * motor->control_timer->Instance->ARR;

    HAL_TIM_OC_Stop(motor->control_timer, channel);
    HAL_TIM_PWM_Stop(motor->control_timer, channel);
    HAL_TIMEx_OCN_Stop(motor->control_timer, channel);
    HAL_TIMEx_PWMN_Stop(motor->control_timer, channel);

    const TIM_OC_InitTypeDef config = {
        .OCMode = mode,
        .Pulse = pulse,
        .OCPolarity = TIM_OCPOLARITY_HIGH,
        .OCNPolarity = TIM_OCNPOLARITY_HIGH,
        .OCFastMode = TIM_OCFAST_DISABLE,
        .OCIdleState = TIM_OCIDLESTATE_RESET,
        .OCNIdleState = TIM_OCNIDLESTATE_RESET,
    };
    HAL_TIM_OC_ConfigChannel(motor->control_timer, &config, channel);

    HAL_TIM_OC_Stop(motor->control_timer, channel);
    HAL_TIMEx_OCN_Start(motor->control_timer, channel);
}

static void shutdown(const motor_t *motor) {
    HAL_TIM_Base_Stop(motor->commut_timer);
    HAL_TIM_Base_Stop_IT(motor->control_timer);
    HAL_ADCEx_InjectedStop_IT(motor->bemf_adc);

    HAL_TIM_OC_Stop(motor->control_timer, TIM_CHANNEL_1);
    HAL_TIM_OC_Stop(motor->control_timer, TIM_CHANNEL_2);
    HAL_TIM_OC_Stop(motor->control_timer, TIM_CHANNEL_3);

    HAL_TIMEx_OCN_Stop(motor->control_timer, TIM_CHANNEL_1);
    HAL_TIMEx_OCN_Stop(motor->control_timer, TIM_CHANNEL_2);
    HAL_TIMEx_OCN_Stop(motor->control_timer, TIM_CHANNEL_3);

    HAL_TIM_PWM_Stop(motor->control_timer, TIM_CHANNEL_1);
    HAL_TIM_PWM_Stop(motor->control_timer, TIM_CHANNEL_2);
    HAL_TIM_PWM_Stop(motor->control_timer, TIM_CHANNEL_3);

    HAL_TIMEx_PWMN_Stop(motor->control_timer, TIM_CHANNEL_1);
    HAL_TIMEx_PWMN_Stop(motor->control_timer, TIM_CHANNEL_2);
    HAL_TIMEx_PWMN_Stop(motor->control_timer, TIM_CHANNEL_3);
}

static void state_change(motor_t *motor, const motor_state_t new) {
    const uint32_t time = HAL_GetTick();

    motor->state = new;
    motor->state_start_time = time;
}

static bool software_timer(uint32_t *prev, const uint32_t time, const uint32_t period) {
    if((time - *prev) >= period) {
        *prev = time;
        return true;
    }

    return false;
}

void motor_init(motor_t *motor) {
    motor->state = MOTOR_STATE_IDLE;
    motor->step = 0;
    motor->pulse = 0;
    motor->vel = 0;
    motor->vel_setpoint = 0;

    shutdown(motor);
}
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

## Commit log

2024-10-15 sine control PWM
2024-10-28 start of hardware design
    [controller.kicad_pcb, controller.kicad_sch, microcontroller.kicad_sch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]
2024-10-28 add IMU, FLOW, 5V, 3.3V, MOSFET SW
    [controller.kicad_sch, microcontroller.kicad_sch, power.kicad_sch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]
2024-10-30 power stage development #1
    [controller.kicad_sch, motor1.kicad_sch]
2024-10-31 remove current sensing, external MOSFET diodes, BEMF filteringadd MOSFETs
    [motor1.kicad_sch]
2024-11-01 uC pinout and second power stage
    [controller.kicad_sch, microcontroller.kicad_sch, motor2.kicad_sch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]
2024-11-01 remove current from architecture
2024-11-01 change P-MOSFET on the battery enter
    [controller.kicad_sch, hog1.kicad_sch, hog2.kicad_sch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]
2024-11-03 footprints, layout
    [controller.kicad_pcb, controller.kicad_sch, hog1.kicad_sch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]
2024-11-05 add VBUS sense to STM and ESP, change buttons and sw to vertical, add USB-C to SEM
    [controller.kicad_pcb, controller.kicad_sch, hog1.kicad_sch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]
2024-11-05 fix voltage divider
    [power.kicad_sch]
2024-11-06 USBLC6, IR2101
    [controller.kicad_pcb, hog1.kicad_sch, hog2.kicad_sch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]
2024-11-06 custom footprints with all 3D models
    [controller.kicad_pcb, hog1.kicad_sch, hog2.kicad_sch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]
2024-11-09 back to LM2105, remove USB-C from STM
    [controller.kicad_pcb, hog1.kicad_sch, hog2.kicad_sch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]
2024-11-09 update date
    [controller.kicad_sch, hog1.kicad_sch, hog2.kicad_sch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]
2024-11-09 first real layout, change comps to MCP6541
    [controller.kicad_pcb, hog1.kicad_sch, hog2.kicad_sch]
2024-11-10 full layout, edge power switch
    [controller.kicad_pcb, hog1.kicad_sch, hog2.kicad_sch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]
2024-11-11 add silkscreen layer
    [controller.kicad_pcb]
2024-11-19 gitignore gerbers and BOM
    [controller.kicad_pcb]
2024-11-27 use diffrent P-MOSFET
    [controller.kicad_pcb, power.kicad_sch]
2024-11-27 bigger capacitors on step down
    [controller.kicad_pcb, power.kicad_sch]
2024-12-08 6 step 100Hz
2024-12-16 add button, G resistors 68ohm, additional 47kohm between G and S
2024-12-23 motor development
2024-12-26 100nF as BEMF filter
2024-12-29 working velocity control
2024-12-31 commut timer with hardware TRGO, single PID
2025-01-04 ESP32C3 UART-HTTP bridge using custom Goose-II protocol
2025-01-04 CMake based project + just STM32CubeMX, fix protocol/DMA modulo BUG
    [cubemx.ioc, main.c, motor.c]
2025-01-05 read battery voltage
2025-01-06 remove unused fragments of protocol, faster ESP communication, fix station UI
    [main.c]
2025-01-06 MessagePack on UART, JSON on network
2025-01-06 UART on 230400, shorter names in JSON
    [cubemx.ioc, main.c]
2025-01-07 firmware work for both motors
2025-01-07 read IMU
2025-01-08 add FLOW sensor
2025-01-11 split serialization and sensors to separate files
2025-01-11 add servos
2025-01-22 fix wheel direction and controls
2025-01-24 UDP+TCP sockets
2025-01-25 faster motors
2025-01-26 improve motor control again
2025-02-22 wip - placement
    [controller.kicad_pcb, controller.kicad_sch, microcontroller.kicad_sch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]
2025-03-08 wip elements
    [controller.kicad_pcb, controller.kicad_sch, microcontroller.kicad_sch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]
2025-03-08 wip routing power stages
    [controller.kicad_pcb, motor1.kicad_sch, motor2.kicad_sch]
2025-03-08 wip - motor and ESP signals
    [controller.kicad_pcb]
2025-03-09 wip better pinout
    [controller.kicad_pcb, controller.kicad_sch, microcontroller.kicad_sch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]
2025-03-09 wip - ready, but need double check
    [controller.kicad_pcb]
2025-03-11 working servos
2025-03-11 flow works
2025-03-12 migrate to kicad 9
    [controller.kicad_sch, microcontroller.kicad_sch, motor1.kicad_sch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]
2025-03-12 check and fix DRC errors
    [controller.kicad_pcb]
2025-03-12 generate schematic in PDF
2025-03-14 state estimation using imu and flow
2025-03-16 python script for visualizer, correct optical flow plot, optical flow gyro-compensation
    [flow.c]
2025-03-16 reset ekf, capacitor on PMW3901
    [stream.c]
2025-03-21 add led datasheet
2025-03-22 ported motors and dead time calculator
2025-03-23 motor 1 work
2025-03-24 switch and ESP work
2025-03-24 port calibration app from Goose-II
2025-03-24 timer timebase
2025-03-26 IMU use calibration values, sending raw and out
2025-03-26 IMU, MAG, FLOW, battery, servos work
2025-03-27 calibration work?
2025-03-28 working FLASH read/write, better ACC calibration sampling
2025-03-28 fix MAG calibration sampling, fix EKF reset yaw
2025-03-30 bidirectional BLDC, actuator setpoint validation, correct actuator directions like in mathematical model
    [dynamixel.c, motor.c, motors.c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]
2025-03-30 fix motor dir in trajectory
2025-04-05 work driftless q=Gn full model
    [main.cpp]
2025-04-05 JPTD for FULL not work, JPTD for JPTD work little bit
    [main.cpp]
2025-04-20 check DATA READY flag when reading OPTICAL FLOW
2025-04-21 add servo offsets in CONFIG
2025-04-24 new servo calibration method? NEED test with JPTD
2025-04-29 controller JPTD 1D and naive, FIX INTEGRATION DT, separate trajectory, separate integrator
    [controller_jptd_dynamic.c, main.cpp, motors.c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]
2025-05-02 partial calibration read/write
2025-05-12 PID controller just works
2025-05-14 clear PID cascade implementation, filter, step experiments, ready for tests
2025-05-14 add PID autotune script
2025-05-16 PID autotuner script
2025-05-17 autotunning PIDs for motors
2025-05-17 smooth lemistate inner PI outer PI no filter
2025-05-17 better PID lambda method for integrating plant
2025-05-21 fix motor vel number of pole pairs
    [motor.c]
2025-05-23 higher optical flow, new KAVAN motors, maybe EKF will work
2025-05-23 add motors step record
2025-05-26 plastic wheels
2025-05-26 plastic wheels steps
2025-05-26 EKF fixed? IMU and MAG fixed 400kHz I2C
    [cubemx.ioc, imu.c, mag.c]
2025-05-27 PID cascade works PERFECTLY
2025-05-27 turn off brown-out detection in ESP32C3
2025-06-04 align J8 and J12 on schematic
    [motor1.kicad_sch, motor2.kicad_sch]
2025-06-07 print also inertial end
2025-06-09 print matrices for dynamic linearization
2025-06-13 renaming to amtch thesis, PID with Tu transform, LISSAJOUS trajectory from Joniak
2025-06-13 better outer Y tunning, fix lissajous
    [controller_cascade_pid.c]
2025-06-13 fix motors velocity plotting
    [controller_cascade_pid.c, motor.c, motors.c]
2025-06-14 add servo offset to telemetry
2025-06-19 remove motion capture from schematic

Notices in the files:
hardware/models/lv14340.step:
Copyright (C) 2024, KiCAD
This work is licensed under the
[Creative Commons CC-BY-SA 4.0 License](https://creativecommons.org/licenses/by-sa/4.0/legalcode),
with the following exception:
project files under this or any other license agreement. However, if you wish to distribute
